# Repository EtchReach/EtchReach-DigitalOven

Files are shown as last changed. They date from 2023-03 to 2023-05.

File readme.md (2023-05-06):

# Smart Oven Project

A project by Enable, a student-led interest group under Nanyang Technology University’s Renaissance Engineering Programme focused on developing assistive technologies for various community partners.

[Product Demonstration](https://youtu.be/oCnXw7KCxz4)
## Overview
Project information and prototype usage can be found [here](https://docs.google.com/document/d/1T6A8cfehCGghUUyGrNWb8jcuDFIxB7nuweHgq2GrgUs/edit?usp=sharing).

## Hardware
### Control Box
CAD files for the control box with its associated components are found in the [Hardware Directory](./Hardware/). Either PLA or PETG filament is suitable.

### Oven Modification
* Dismantle the oven and identify the wires connected to the oven's components (Heating Coil, Rotisserie, Fan, Bulb).
* Connect the thermal fuse to the wires connecting to the heating coil(s).
* Based on the bulb's voltage requirements, attach the appropriate power resistor. (Power resistor is able to withstand the higher temperatures).
* Extend the wires to the 8 Channel Relay using the 14AWG wires.
* Connect the normally closed end of the 8 Channel Relay to a 3 pin plug.
* Heat shrink exposed ends.
* Reassemble the oven.

### Oven Connection Diagram:


## Software
### Communication Overview:
REACH Enable Schematic pptx (2)

Bi-directional communication between devices and the websocket server running on the ESP32 micro-controller is enabled through a WiFi router.

### Oven Control Logic
The software logic to control the various components of the oven was done with the [Arduino](https://www.arduino.cc/) programming language. The Arduino file can be found [here](./webSocket2/webSocket2.ino).

Other than interfacing with the various hardware components of the Oven, such as the thermoprobe and the OLED display module, the Arduino code also hosts the websocket server to process inputs from the web application frontend and send the neccesary information back to the application.

### User-Interfacing Frontend
The web application frontend was created using HTML, CSS and Javascript. The files can be found [here](./webSocket2/data/). These HTML, CSS and Javascript files were uploaded into the ESP32 via the Serial Peripheral Interface Flash File System (SPIFFS). Tutorial to upload via SPIFFS can be found [here](https://randomnerdtutorials.com/esp32-web-server-spiffs-spi-flash-file-system/).

The web application is responsible for displaying various information to the end-user, such as the currently running oven function, duration left, and the oven's current temperature. Users will also be able to configure the temperature and duration for each of the three oven functionality (Grill, Bake and Rotisserie) via the settings page.

An additional file (Credential.h) needs to be included in [this directory](./webSocket2). It contains 2 variables of mySSID and myPASSWORD which is the WiFi router's name and password respectively.

## Electronics
### Wiring
* Connect the electrical components based on the wiring schema:
REACH Enable Schematic pptx (1)

## Bill of Materials
|Item|Quantity|Purpose|
|:-|:-:|:-|
|Conventional Oven|1|To be modified||
|ESP32|1|Micro-Controller|
|Micro USB Cable|1|To power and program micro-controller|
|PT100 Temperature Probe|1|To measure temperature changes|
|MAX31865 Module|1|To process the oven's temperature|
|OLED Display Module 0.96" |1|To display commands|
|Donut Board|1|To mount micro-controller|
|8 Chanel Relay|1|To control the oven's functionalities|
|220Ω Power Resistor|1|To reduce Voltage to the oven's bulb|
|250C 10A Thermal Fuse|2|Safety mechanism to prevent overheating|
|Wire Splitter|2|To split cables into parallel circuits|
|Heat Shrink Tube|As Required|To insulate exposed ends|
|14 AWG Wires|As Required|To connect |
|Jumper Cables|As Required|To connect electronic components|
|Cable Ties|As Required|For cable management|

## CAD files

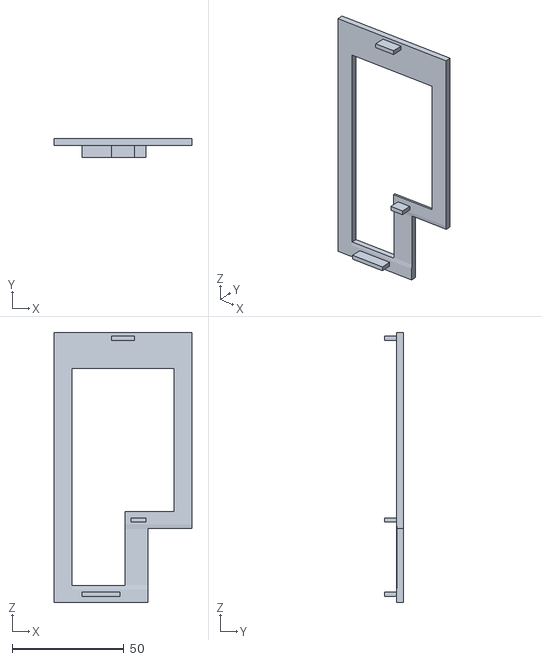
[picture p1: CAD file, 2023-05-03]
Hardware/Component_Holder.STL
61.6 x 8.30 x 120.6

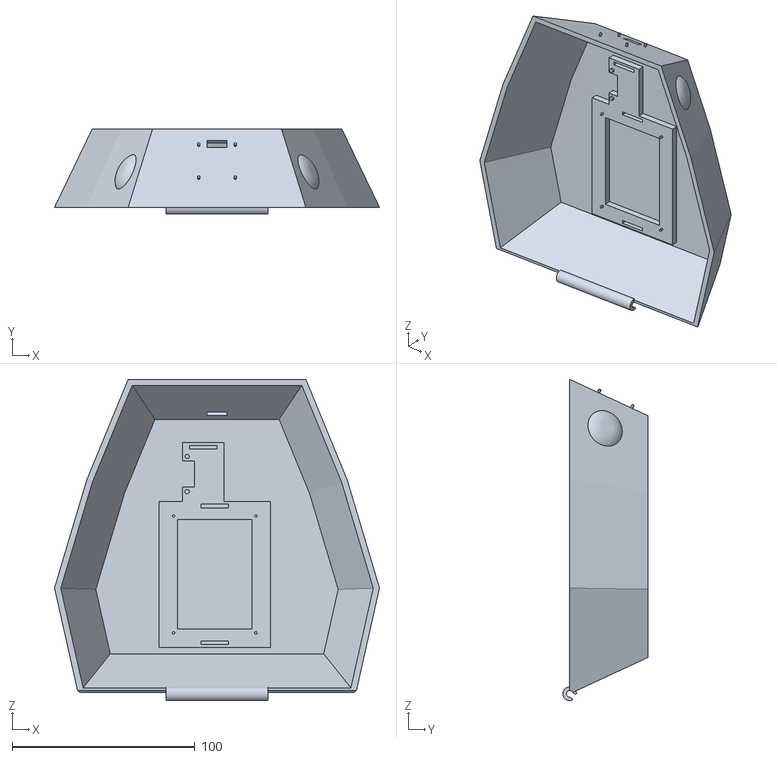
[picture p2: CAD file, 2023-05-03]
Hardware/Casing_Bottom.STL
178.0 x 46.7 x 176.0

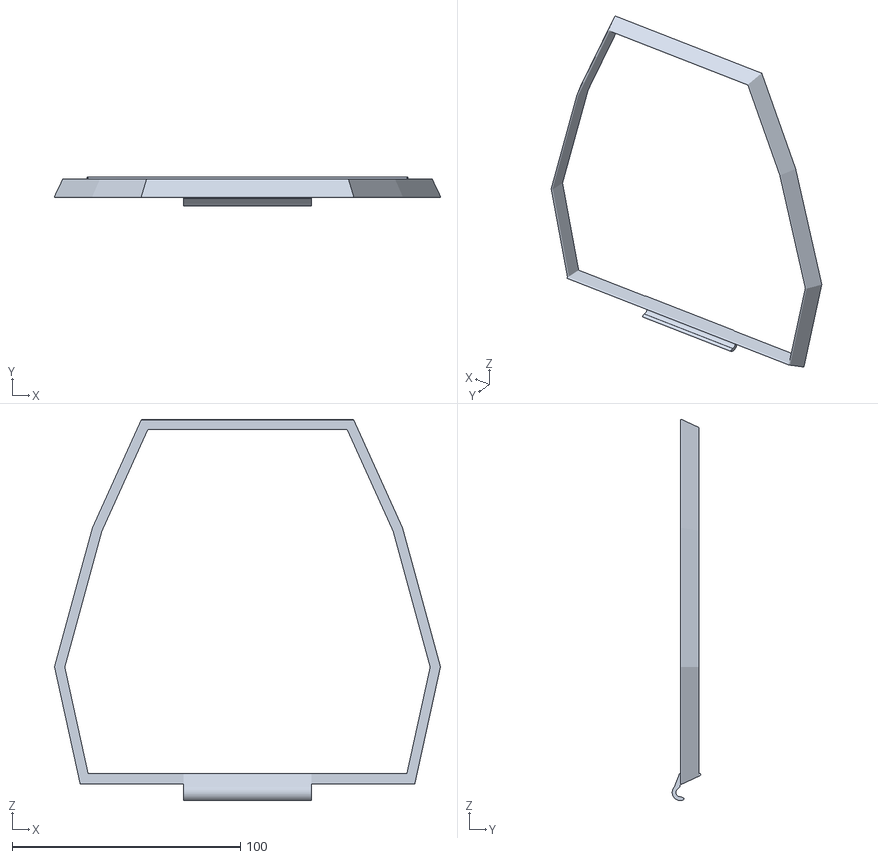
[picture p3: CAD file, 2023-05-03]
Hardware/Hinge_Bottom.STL
169.1 x 12.5 x 166.9

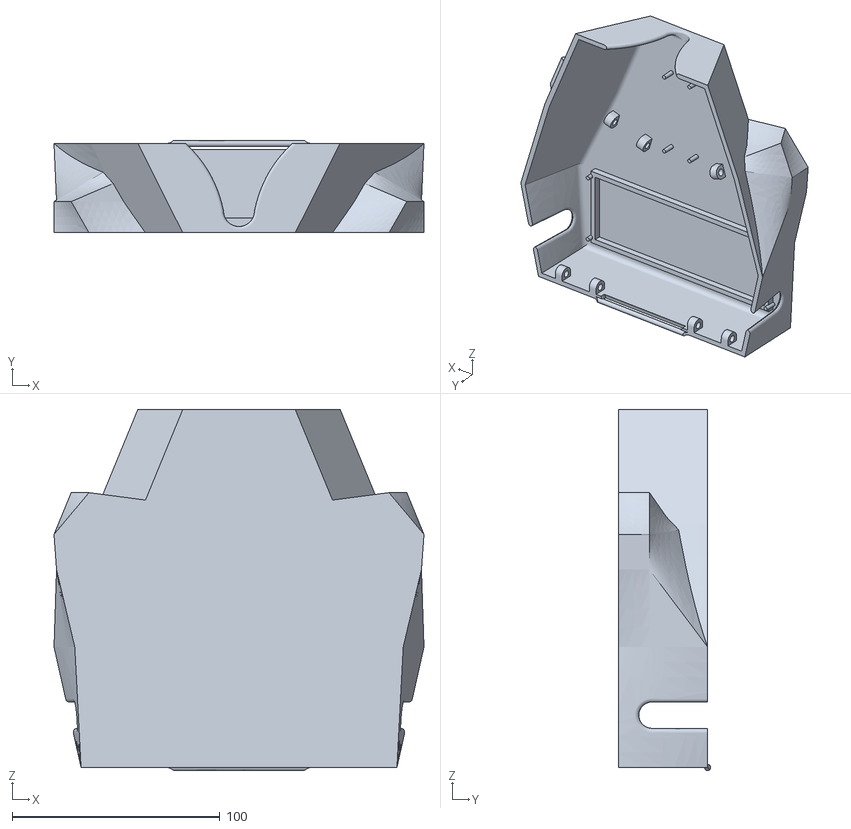
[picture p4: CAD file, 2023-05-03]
Hardware/Casing_Top.STL
178.0 x 44.5 x 173.8

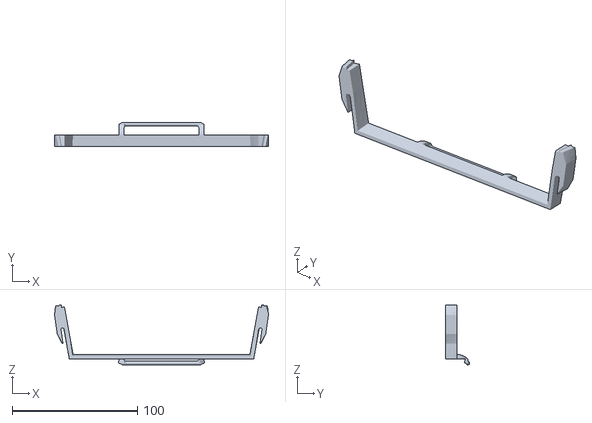
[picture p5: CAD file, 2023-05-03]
Hardware/Hinge_Top.STL
171.1 x 19.5 x 47.9

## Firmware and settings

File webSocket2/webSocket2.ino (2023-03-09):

/*********
  references:
  https://randomnerdtutorials.com/esp32-websocket-server-arduino/#1
  https://randomnerdtutorials.com/esp32-web-server-spiffs-spi-flash-file-system/
*********/

// Websocket
#include <WiFi.h>
#include <AsyncTCP.h>
#include <ESPAsyncWebServer.h>
#include "SPIFFS.h"
#include "Credentials.h"

// Oven
#include <SPI.h>
#include <Wire.h>
#include <Keypad.h>
#include <Adafruit_GFX.h>
#include <Adafruit_SSD1306.h>
#include <Adafruit_MAX31865.h>

// KEYPAD constants & variables
#define ROW_NUM 4    // four rows
#define COLUMN_NUM 3 // three columns

char keys[ROW_NUM][COLUMN_NUM] = {
    {'1', '2', '3'},
    {'4', '5', '6'},
    {'7', '8', '9'},
    {'*', '0', '#'}};

byte pin_rows[ROW_NUM] = {13, 12, 14, 27};  // GIOP18, GIOP5, GIOP17, GIOP16 connect to the row pins
byte pin_column[COLUMN_NUM] = {26, 25, 33}; // GIOP4, GIOP0, GIOP2 connect to the column pins

using namespace std;

Keypad keypad = Keypad(makeKeymap(keys), pin_rows, pin_column, ROW_NUM, COLUMN_NUM);

// OLED constants & variables
#define SCREEN_WIDTH 128 // OLED display width, in pixels
#define SCREEN_HEIGHT 32 // OLED display height, in pixels

#define OLED_RESET 4        // Reset pin # (or -1 if sharing Arduino reset pin)
#define SCREEN_ADDRESS 0x3C ///< See datasheet for Address; 0x3D for 128x64, 0x3C for 128x32
Adafruit_SSD1306 display(SCREEN_WIDTH, SCREEN_HEIGHT, &Wire, OLED_RESET);

// Thermoprobe: Use software SPI: CS, DI, DO, CLK
Adafruit_MAX31865 thermo = Adafruit_MAX31865(05, 23, 19, 18);

// The value of the Rref resistor. Use 430.0 for PT100 and 4300.0 for PT1000
#define RREF 430.0
// The 'nominal' 0-degrees-C resistance of the sensor
// 100.0 for PT100, 1000.0 for PT1000
#define RNOMINAL 100.0

// relay constants & variables
// bool upper = false;
// bool lower = false;
// bool bulb = false;
// bool fan = false;
// bool rotisserie = false;

// RELAY CONNECTIONS (LEFT -> RIGHT)
// GND
// TX2 GPIO 17 BULB
// RX2 GPIO 16 LOWER COIL
// D2 GPIO 2 UPPER COIL
// D4 GPIO 4 FAN
// D15 GPIO 15 ROTISSERIE
// VIN

const int lowerPin = 16; // RX2 -> IN2 -> LOWER COIL
const int bulbPin = 2; // -> IN3 -> Bulb
const int upperPin = 4; // -> IN4 -> UPPER COIL
const int fanPin = 17; // TX2 -> IN1 -> FAN
const int rotisseriePin = 15; // -> IN5 -> Rotisserie

// thermoprobe constants & variables
float temp = 0;
float readTemp = 0;
unsigned long long prevTempMillis = 0;

// logtime constants
const int timeInterval = 60000;
unsigned long prevTimeMillis = 0;
const long millisToHour = 3600000;
const int millisToMin = 60000;
const int millisToSec = 1000;

// Websocket Settings
bool ledState = 0;
const int ledPin = 2;
String temperature1;
String temperature2;
String temperature3;
String temperature4;
String duration1;
String duration2;
String duration3;
String duration4;
String function1;
String function2;
String function3;
String function4;

bool wsConnected = false;

// Websocket read values
String receivedFunction = "0";
String receivedTemp = "0";
String receivedDuration = "0";

// Websocket send values
unsigned long long last_send = 0;
const int sendInterval = 10000;

// Main loop values
unsigned long long last_time = 0;
unsigned long long current_time = 0;

// Create AsyncWebServer object on port 80
AsyncWebServer server(80);
AsyncWebSocket ws("/ws");

void resetOven() {
  current_time = millis();
  last_time = millis();
  receivedFunction = "0";
  receivedTemp = "0";
  receivedDuration = "0";
  digitalWrite(upperPin, HIGH);
  digitalWrite(lowerPin, HIGH);
  digitalWrite(fanPin, HIGH);
  digitalWrite(rotisseriePin, HIGH);
  digitalWrite(bulbPin, HIGH);
  notifyClients();
}

// callback to handle the data from clients via websocket protocol
void handleWebSocketMessage(void *arg, uint8_t *data, size_t len) { 
  AwsFrameInfo *info = (AwsFrameInfo *)arg;
  if (info->final && info->index == 0 && info->len == len && info->opcode == WS_TEXT)
  {
    data[len] = 0;
    Serial.printf("%s\n", (char *)data);
    char *ptr;
    ptr = strtok((char *)data, ",");
    Serial.println(String(ptr));
    if (strcmp((char *)ptr, "function") == 0) {
      receivedFunction = String(strtok(NULL, ","));
      receivedTemp = String(strtok(NULL, ","));
      receivedDuration = String(strtok(NULL, ","));
      last_time = millis();
      last_send = 0;
    } else if (strcmp((char *)ptr, "save") == 0) {
      Serial.printf("Saving Configurations\n");
      char *settings = strtok(NULL, ",");
      Serial.printf("%s\n", settings);
      savePresets(settings);
      loadPresets();
      return;
    } else if (strcmp((char*)ptr, "reset") == 0) {
      resetOven();
    } else {
      while (ptr != NULL) {
        Serial.println(ptr);
        ptr = strtok(NULL, ",");
      }
    }
  }
}

// configure event listener to handle different WebSocket protocol
void onEvent(AsyncWebSocket *server, AsyncWebSocketClient *client, AwsEventType type,
             void *arg, uint8_t *data, size_t len)
{
  switch (type)
  {
  case WS_EVT_CONNECT:
    Serial.printf("WebSocket client #%u connected from %s\n", client->id(), client->remoteIP().toString().c_str());
    wsConnected = true;
    break;
  case WS_EVT_DISCONNECT:
    Serial.printf("WebSocket client #%u disconnected\n", client->id());
    wsConnected = false;
    break;
  case WS_EVT_DATA: // when a data packet is received from the client
    handleWebSocketMessage(arg, data, len);
    break;
  case WS_EVT_PONG:
  case WS_EVT_ERROR:
    break;
  }
}

// initialises websocket protocol
void initWebSocket()
{
  ws.onEvent(onEvent);
  server.addHandler(&ws);
}

// Searches for placeholders in HTML and replaces them before sending the webpage to the browser
String processor(const String &var)
{
  Serial.println(var);
  if (var == "STATE")
  {
    if (ledState)
    {
      return "ON";
    }
    else
    {
      return "OFF";
    }
  }
  else if (var == "defaultT1")
  {
    return temperature1;
  }
  else if (var == "defaultT2")
  {
    return temperature2;
  }
  else if (var == "defaultT3")
  {
    return temperature3;
  }

  else if (var == "defaultD1")
  {
    return duration1;
  }
  else if (var == "defaultD2")
  {
    return duration2;
  }
  else if (var == "defaultD3")
  {
    return duration3;
  }
  return "";
}

void savePresets(char *data)
{
  File file = SPIFFS.open("/text.txt", "w");
  if (!file)
  {
    Serial.println("Error opening file for writing");
    return;
  }
  int bytesWritten = file.print(data);
  if (bytesWritten > 0)
  {
    Serial.println("File was written");
    Serial.println(bytesWritten);
  }
  else
  {
    Serial.println("File write failed");
  }
  file.close();
  return;
}

void loadPresets()
{ // read preset configurations
  File file = SPIFFS.open("/text.txt");
  if (!file)
  {
    Serial.println("Failed to open file for reading");
    return;
  }
  vector<String> v;
  while (file.available())
  {
    v.push_back(file.readStringUntil('\n'));
  }
  file.close();
  for (String s : v)
  {
    Serial.println(s);
  }
  temperature1 = v[0];
  duration1 = v[1];

  temperature2 = v[2];
  duration2 = v[3];

  temperature3 = v[4];
  duration3 = v[5];
}

void setup()
{
  Serial.begin(115200);

  // Initialize SPIFFS
  if (!SPIFFS.begin(true))
  {
    Serial.println("An Error has occurred while mounting SPIFFS");
    return;
  }

  loadPresets();

  // Connect to Wi-Fi
  WiFi.begin(mySSID, myPASSWORD);
  while (WiFi.status() != WL_CONNECTED)
  {
    delay(1000);
    Serial.println("Connecting to WiFi..");
  }

  // Print ESP Local IP Address
  Serial.println(WiFi.localIP());

  initWebSocket();
//  Routing for root / web page
  server.on("/", HTTP_GET, [](AsyncWebServerRequest *request)
            { request->send(SPIFFS, "/index.html", String(), false, processor); });
//  // Route to load style.css file
//  server.on("/style.css", HTTP_GET, [](AsyncWebServerRequest *request)
//            { request->send(SPIFFS, "/style.css", "text/css"); });
            
  server.serveStatic("/", SPIFFS, "/").setDefaultFile("index.html");

  // Start server
  server.begin();

  // Oven Setup
  pinMode(upperPin, OUTPUT);
  pinMode(lowerPin, OUTPUT);
  pinMode(fanPin, OUTPUT);
  pinMode(rotisseriePin, OUTPUT);
  pinMode(bulbPin, OUTPUT);

  digitalWrite(upperPin, HIGH);
  digitalWrite(lowerPin, HIGH);
  digitalWrite(fanPin, HIGH);
  digitalWrite(rotisseriePin, HIGH);
  digitalWrite(bulbPin, HIGH);

  Serial.begin(115200);

  thermo.begin(MAX31865_3WIRE); // set to 2WIRE or 4WIRE as necessary, initialising thermoprobe
  
  // SSD1306_SWITCHCAPVCC = generate display voltage from 3.3V internally
  if (!display.begin(SSD1306_SWITCHCAPVCC, SCREEN_ADDRESS))
  {
    Serial.println(F("SSD1306 allocation failed"));
    for (;;)
      ; // Don't proceed, loop forever
  }

  // Clear the buffer
  display.clearDisplay();
  display.setTextColor(WHITE);
  display.setTextSize(1);
  display.display();
}

float getTemperature()
{
  uint16_t rtd = thermo.readRTD();

//  Serial.print("RTD value: "); Serial.println(rtd);
  float ratio = rtd;
  ratio /= 32768;
//  Serial.print("Ratio = "); Serial.println(ratio,8);
//  Serial.print("Resistance = "); Serial.println(RREF*ratio,8);
//  Serial.print("Temperature = "); Serial.println(thermo.temperature(RNOMINAL, RREF));

  // Check and print any faults
  uint8_t fault = thermo.readFault();
  if (fault) {
    Serial.print("Fault 0x");
    Serial.println(fault, HEX);
    if (fault & MAX31865_FAULT_HIGHTHRESH) {
      Serial.println("RTD High Threshold");
    }
    if (fault & MAX31865_FAULT_LOWTHRESH) {
      Serial.println("RTD Low Threshold");
    }
    if (fault & MAX31865_FAULT_REFINLOW) {
      Serial.println("REFIN- > 0.85 x Bias");
    }
    if (fault & MAX31865_FAULT_REFINHIGH) {
      Serial.println("REFIN- < 0.85 x Bias - FORCE- open");
    }
    if (fault & MAX31865_FAULT_RTDINLOW) {
      Serial.println("RTDIN- < 0.85 x Bias - FORCE- open");
    }
    if (fault & MAX31865_FAULT_OVUV) {
      Serial.println("Under/Over voltage");
    }
    thermo.clearFault();
  }
  Serial.println();
  return (thermo.temperature(RNOMINAL, RREF));
}

void monitorTemperature(bool bottomCoil) {
  readTemp = getTemperature();
  temp = (float)(receivedTemp.toInt());
  //Serial.println(readTemp);
  if (readTemp < temp) {
    digitalWrite(upperPin, LOW);
    if (bottomCoil) {
      digitalWrite(lowerPin, LOW);
    }
  }
  else {
    digitalWrite(upperPin, HIGH);
    digitalWrite(lowerPin, HIGH);
  }
}

void notifyClients() {
  int durationElapsed = current_time - last_time;
  ws.textAll("temperature," + String(readTemp) + ",duration," + String(durationElapsed / (1000 * 60)) + ",receivedTemp," + String(receivedTemp)+ ",receivedDuration," + String(receivedDuration)+ ",receivedFunction," + String(receivedFunction));
}

void loop() {
  int totalDuration = receivedDuration.toInt() * 1000 * 60;
  int durationElapsed = current_time - last_time;
  int function = receivedFunction.toInt();

  // function != 0 => start oven
  if (function != 0) {
    current_time = millis();

    // function == "1" => Grill => Bulb on, Top and Bottom Coil
    // function == "2" => Bake => Bulb on, Top and Bottom Coil, Fan
    // function == "3" => Rotisserie => Bulb on, Top and Bottom Coil, Rotisserie

    display.clearDisplay();
    display.setCursor(0,0);

    switch (function) {
      case 1:
        digitalWrite(bulbPin, LOW);
        monitorTemperature(true);
        display.println("Grill");
        break;

      case 2:
        digitalWrite(bulbPin, LOW);
        digitalWrite(fanPin, LOW);
        monitorTemperature(true);
        display.println("Bake");
        break;
  
      case 3:
        digitalWrite(rotisseriePin, LOW);
        digitalWrite(bulbPin, LOW);
        monitorTemperature(true);
        display.println("Rotisserie");
        break;
  
      default:
        resetOven();
        display.println("Unknown function");
        break;
    }

    display.println("--------------------");
    display.println("Temp: " + String(readTemp) + "/" + receivedTemp);
    display.println("Duration: " + String(durationElapsed / (1000 * 60)) + "/" + receivedDuration);
    display.display();

    Serial.println("Current Time: " + String(current_time) + " | Last Time: " + String(last_time) + " | durationElapsed: " + String(durationElapsed) + " | totalDuration: " + String(totalDuration));

    if (current_time - last_send >= sendInterval) {
      last_send = current_time;
      notifyClients();
    }

    if (durationElapsed >= totalDuration) {
      last_send = current_time;
      resetOven();
    }
  } else { // function == "0" => stop oven
    resetOven();
    display.clearDisplay();
    display.setCursor(0,0);
    if (wsConnected) {
      display.println("");
      display.println("Select a Function to start!");
    } else {
      display.println("Connect to the");
      display.println("Smart Oven at: ");
      display.println(WiFi.localIP());
    }
    display.display();
  }

  ws.cleanupClients(); // limits number of clients by closing oldest client when maximum num of client has exceeded - can call once per second to conserve power
}

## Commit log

2022-11-23 Add communication from esp32 to ws
2022-11-23 reset button
2022-11-23 fixed temp and changed limits
    [webSocket2.ino]
2022-11-29 comment play button
2023-01-26 For hui xiang to add info button
2023-01-27 added padding to buttons
2023-02-09 added visbilities for buttons
2023-02-09 Add temperature and duration states
2023-03-16 Rename Bottom Buttons
2023-03-16 add start-stop button
2023-05-03 cad files
    [Casing_Bottom.STL, Casing_Top.STL, Component_Holder.STL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]
